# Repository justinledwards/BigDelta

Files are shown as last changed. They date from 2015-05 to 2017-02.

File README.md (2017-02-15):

# BigDelta

A very large Delta 3D printer with very high precision and reliability that makes beautiful and accurate prints.
Chat at irc://chat.freenode.net/bigdelta

BOM: https://goo.gl/YLESNC
Mostly EU sourced BOM: https://goo.gl/JueIIJ

The Pudding: https://goo.gl/photos/vQzHpMG1wdQYkDLd6  

**Tools required:**
M5 tap, some oil for tapping.  M5 and M3 allen wrenches.  Wire cutters / strippers. 

**Recent:**
Added versions for 2040 Verticals and 4040 verticals.  Horizontal extrusion should be at 2040 for either.

**Tips:**
Instead of buying 1500mm x 2 for the horizontal extrusions you can buy 500mm x 6 to save some cutting.

**Onshape (CAD Files):**
https://goo.gl/xjHlLQ
https://goo.gl/zTKVrY

**Idler-nut-mod Onshape**
https://goo.gl/oGXj6e

**Build Photos:**
https://goo.gl/NL6L4Y
https://goo.gl/photos/2pFiowiZTJBhTSM98

----------

|Frame and Fastners|Quantity|Price Each|Price|Link|Notes|
| --- | --- | --- | --- | --- | --- |
|Solid Wheel Kit|9|$4.85|$43.65|http://openbuildspartstore.com/solid-v-wheel-kit/||
|Wheel Bolts 30mm M5 (25 pack)|1|$4.35|$4.35|http://openbuildspartstore.com/low-profile-screws-m5/||
|6mm Alu Spacers|6|$0.20|$1.20|http://openbuildspartstore.com/aluminum-spacers/||
|Eccentric spacers full size 6mm|3|$2.00|$6.00|http://openbuildspartstore.com/eccentric-spacer/||
|80mm gantry plate|3|$12.00|$36.00|http://openbuildspartstore.com/v-slot-gantry-plates/||
|1500mm 2040 extrusion|5|$19.50|$97.50|http://openbuildspartstore.com/v-slot-linear-rail/|Can get black or silver in 2040, 4040 vertices are available as well as 2040\. You can use 4040 for more rigidity|
|Endstops|3|$4.50|$13.50|http://openbuildspartstore.com/micro-limit-switch-kit-with-mounting-plate/|reliable and highly repeatable|
|Long vertex bolts 40mm M5 (25 pack)|1|$4.90|$4.90|http://openbuildspartstore.com/low-profile-screws-m5/|Doesn't hurt to buy an extra pack|
|Short vertex bolts 10mm M5 (25 pack)|2|$3.15|$6.30|http://openbuildspartstore.com/low-profile-screws-m5/|Again doesn't hurt to buy extra|
|18" Glass Build Plate|1|$47.99|$47.99|http://amzn.to/1Q1Ltjk||
|5 pack of the best steppers|1|$49.99|$49.99|http://www.ebay.com/itm/5pcs-NEMA17-BIPOLAR-STEPPER-MOTOR-76-oz-in-for-3D-Printer-ship-from-chicago-/181582676246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|You'll only need 3, but might as well have extra, you'll find a use for them|
|GT2 belt by the meter|6|$1.80|$10.80|http://www.robotdigg.com/product/10/Open+Ended+6mm+Width+GT2+Belt||
|Idler Pulley|3|$1.80|$5.40|http://www.robotdigg.com/product/383/6mm+wide+belt+idler+pulley+wheel+5mm+bore||
|16 tooth GT2 gear|3|$1.80|$5.40|http://www.robotdigg.com/product/59/Rostock-16-Teeth-5mm-Bore-GT2-Pulley||
|Post assembly T-Nuts (100 pack)|1|$7.50|$7.50|http://www.robotdigg.com/product/237|Not necessary, but makes life a lot easier|
|Pre assembly T-nuts (100 pack)|1|$8.00|$8.00|http://www.robotdigg.com/product/317/Pre+Assembly+T+Nuts+for+2020+Aluminum+Extrusion||
|18" strong rod kit|1|$25.69|$25.69|http://www.tridprinting.com/Mechanical-Parts/#3D-Printer-Rod-Kit||

----------

|Hotend|Quantity|Price Each|Price|||
| --- | --- | --- | --- | --- | --- |
|Genuine J-Head Hotend MK8|1|$56.99|$56.99|https://www.hotends.com/index.php?route=product/product&product_id=88|Specify MK8 in the order comments for the latest model, one of those things you shouldn't go cheap on|
|25mm metal fan|1|$1.80|$1.80|http://www.robotdigg.com/product/318/2510+12V+0.1A+DC+Fan|More never hurts|
|5015 blower parts fan|1|$1.80|$1.80|http://www.robotdigg.com/product/320/5015+12VDC+0.23A+Blower+Fan|More never hurts|

----------

|Extruder|Quantity|Price Each|Price|||
| --- | --- | --- | --- | --- | --- |
|Nema 11 27:1 geared stepper|1|$31.76|$31.76|http://www.omc-stepperonline.com/gear-ratio-271-planetary-gearbox-dual-shaft-nema-11-stepper-11hs120674dpg27-p-133.html|Might want to order 2 since shipping costs a bit|
|Tatsu V2 6mm ID Drive gear|1|$25.00|$25.00|http://deezmaker.com/store/#!/Tatsu-v2-Drive-Gear-Hobbed-Filament-Drive-Gear/p/24043350|Price sounds ridiculous, but it's worth it when you see it and use it, same as above|
|Spearfishing latex tubing|1|$14.23|$14.23|http://amzn.to/1Q1Lwvg||
|PTFE Tubing 4mm OD|1|$8.33|$8.33|http://www.ebay.com/itm/2-meters-PTFE-Teflon-Tube-For-1-75mm-Filament-for-3D-Printer-RepRap-Rostock-/261689172537||

----------

|Make your choice|Quantity|Price Each|Price|||
| --- | --- | --- | --- | --- | --- |
|Smoothieboard|0|$134.97|$0.00|http://shop.uberclock.com/collections/smoothie/products/smoothieboard-4x|Made by the original developers, only 1/16th microstepping|
|Azteeg X5 Mini|0|$109.00|$0.00|http://www.panucatt.com/azteeg_X5_mini_reprap_3d_printer_controller_p/ax5mini.htm|Uses smoothieware, not made by the original developers, a little crowded, but 1/32 microstepping, no networking|

----------
|Others|Quantity|Price Each|Price|||
| --- | --- | --- | --- | --- | --- |
|Zip ties|0|$0.00|$0.00||amazon by the box|
|M3 socket cap screws|||$0.00||amazon by the box|
|M3 nuts and nyloc nuts|||$0.00||amazon by the box|
|Powersupply 12V|0|$0.00|$0.00|http://amzn.to/1LPI4wd|You can use an ATX PSU that you already have, or get a dedicated 12V 30A PSU|
|Good filament 1.75mm PLA 1KG rolls|0|$30.00|$0.00|http://atomicfilament.com/|Check on #reprap on freenode for discounts|
|Glue-All Interior|1|$6.71|$6.71|http://amzn.to/1LPHP46||
|Printed Parts|1|$0.00|||Nearest & Dearest|
|Wires|||||Need 4 wires for each stepper, 2 wires for each endstop, 2 thicker wires for hotend, 2 wires for fans|
|Electronics fan|||||Doesn't hurt to have a fan go over your control board|
|2 part epoxy|||||for building rods|
|**Total**|||**$520.79**|||

PTCs http://amzn.to/1LPHxub

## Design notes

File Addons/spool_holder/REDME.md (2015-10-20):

Required Stuff:

1x Threaded rod (5/16 or 8mm) -- length contingent on extrusion length
2x 608zz Bearings
2x M8 or 5/16 lock nuts
2x M8 or 5/16 nuts

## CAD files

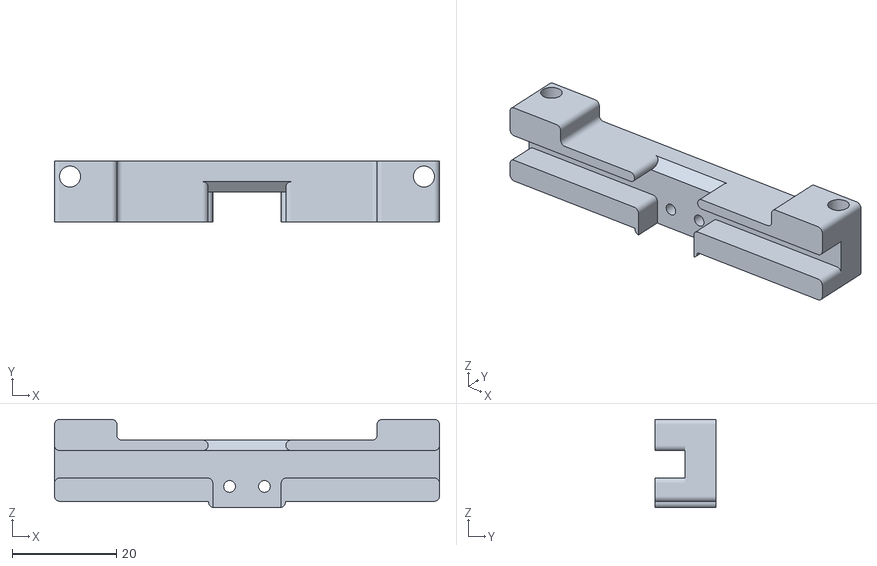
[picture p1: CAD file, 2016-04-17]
Addons/Magnetic_Probe.stl
74.0 x 11.8 x 17.0

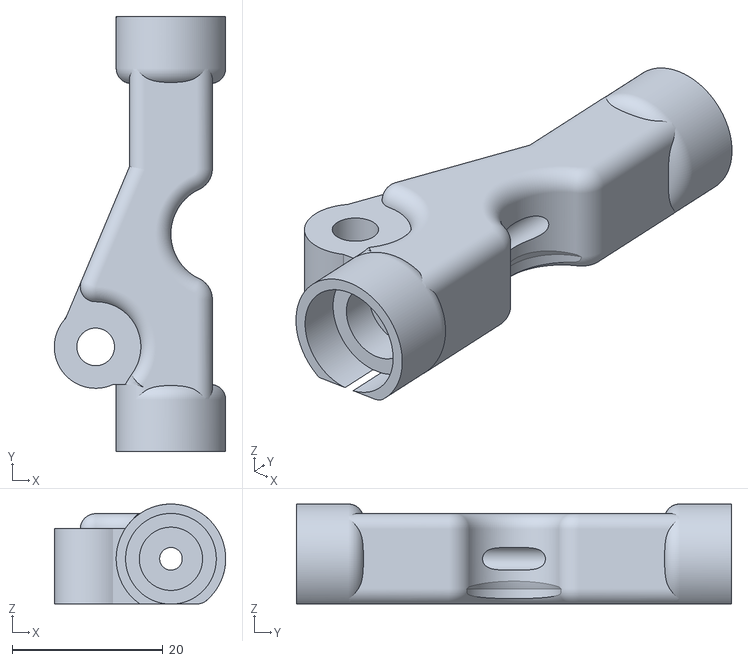
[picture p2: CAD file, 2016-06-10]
Addons/metal_tube_extruder/Rework Metal Tube Extruder - TubeHolder.stl
22.8 x 57.8 x 13.3

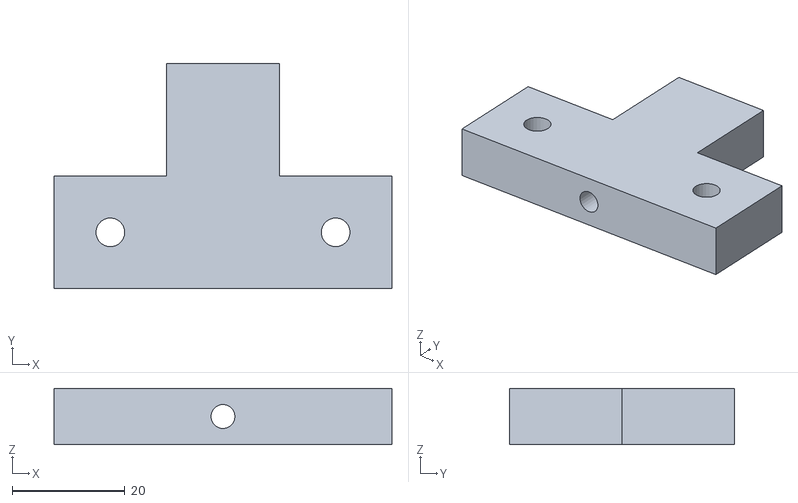
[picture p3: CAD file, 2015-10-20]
Addons/spool_holder/guide.stl
60.0 x 40.0 x 10.0

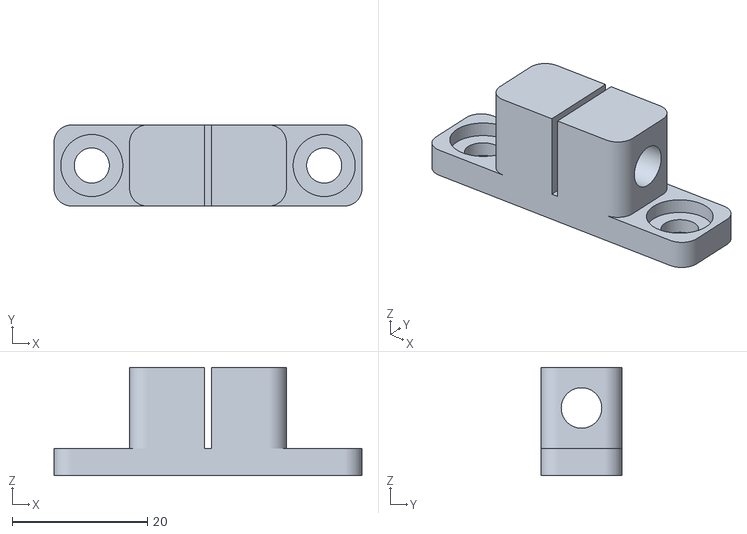
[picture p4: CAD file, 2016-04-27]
Misc-tools/Rod Jigs - Rod Cutter Jig.stl
45.6 x 12.0 x 16.0

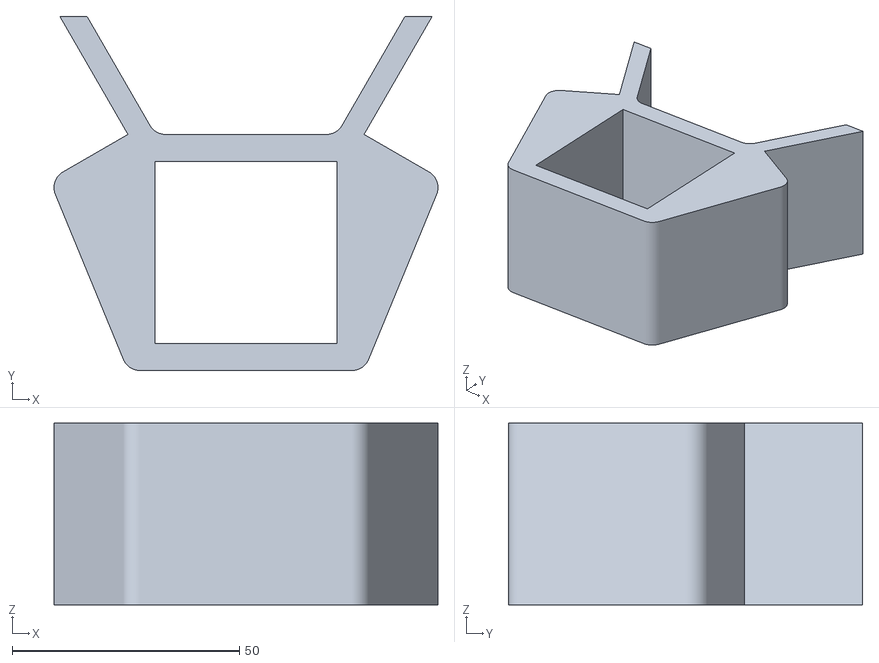
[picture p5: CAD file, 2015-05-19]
original_build/Vertex - Part 1.stl
84.6 x 78.0 x 40.0

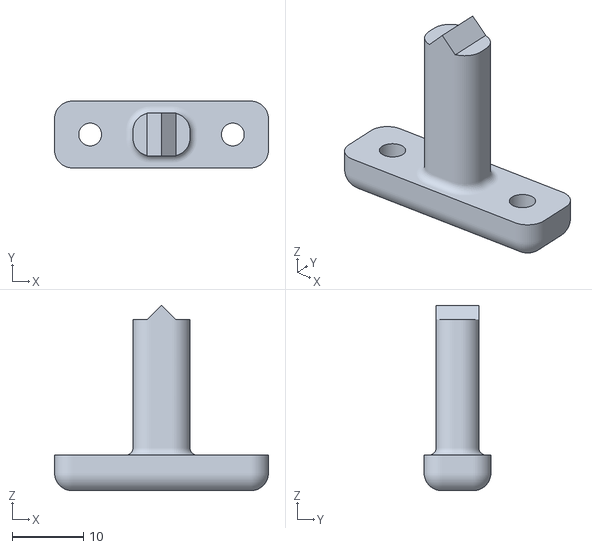
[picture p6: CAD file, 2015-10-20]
Sextruder-Idler.stl
30.0 x 9.38 x 26.0

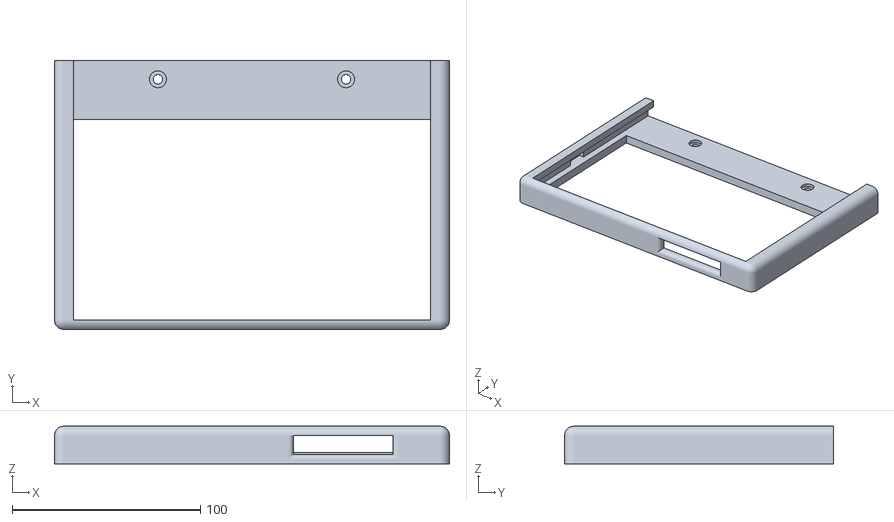
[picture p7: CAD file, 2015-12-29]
Addons/Nexus-7-Holder.stl
210.0 x 143.0 x 20.0

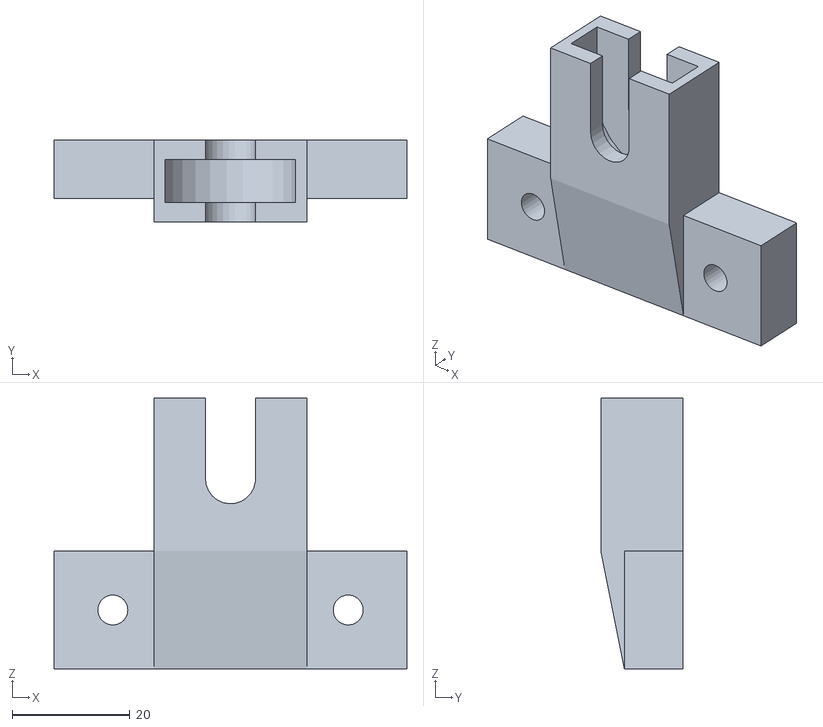
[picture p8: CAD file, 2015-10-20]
Addons/spool_holder/holder_for_extrusion.stl
60.0 x 14.0 x 46.0

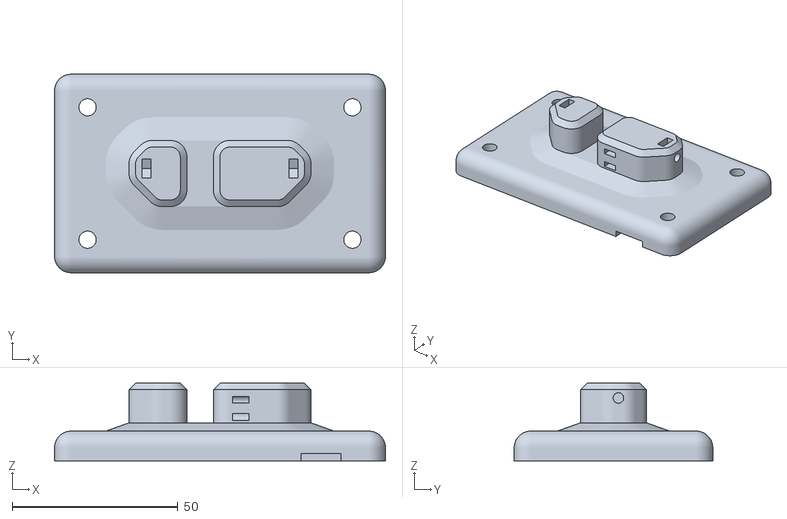
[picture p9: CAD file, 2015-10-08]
Carriage.stl
100.0 x 60.0 x 23.5

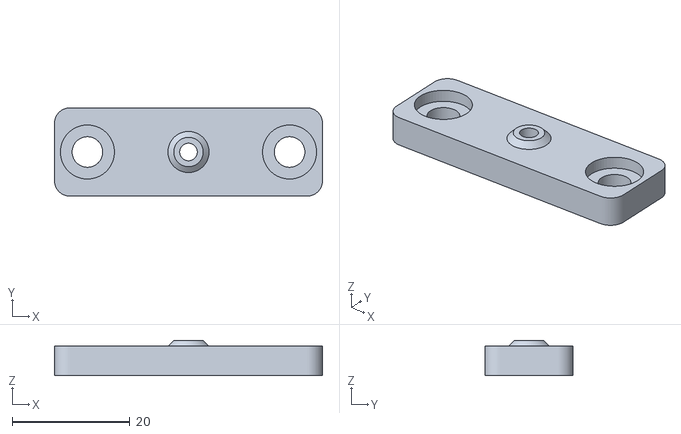
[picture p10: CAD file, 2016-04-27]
Misc-tools/Rod Jigs - Rod Glue Jig.stl
45.6 x 15.0 x 6.00

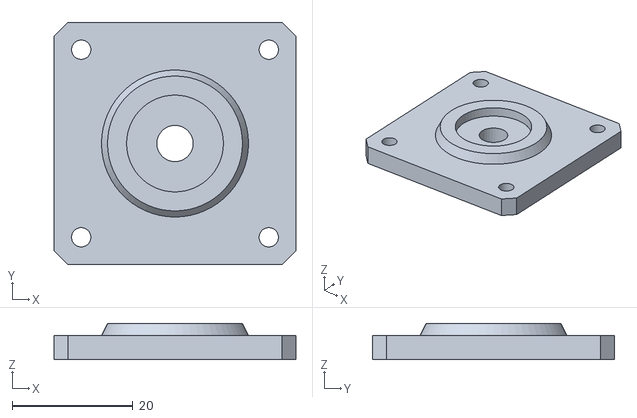
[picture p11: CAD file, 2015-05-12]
original_build/vertex_20x40_idler_cap.stl
40.0 x 40.0 x 6.00

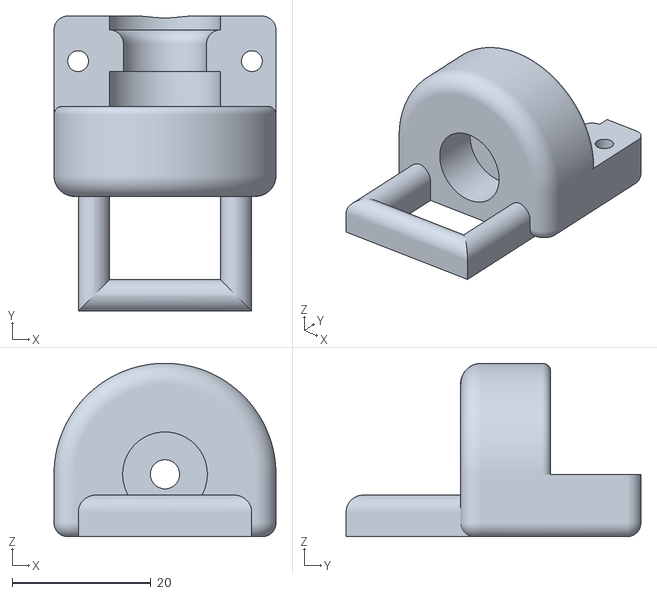
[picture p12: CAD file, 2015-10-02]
Addons/Effector-E3D-Volcano-Clamp.stl
32.0 x 42.5 x 25.0

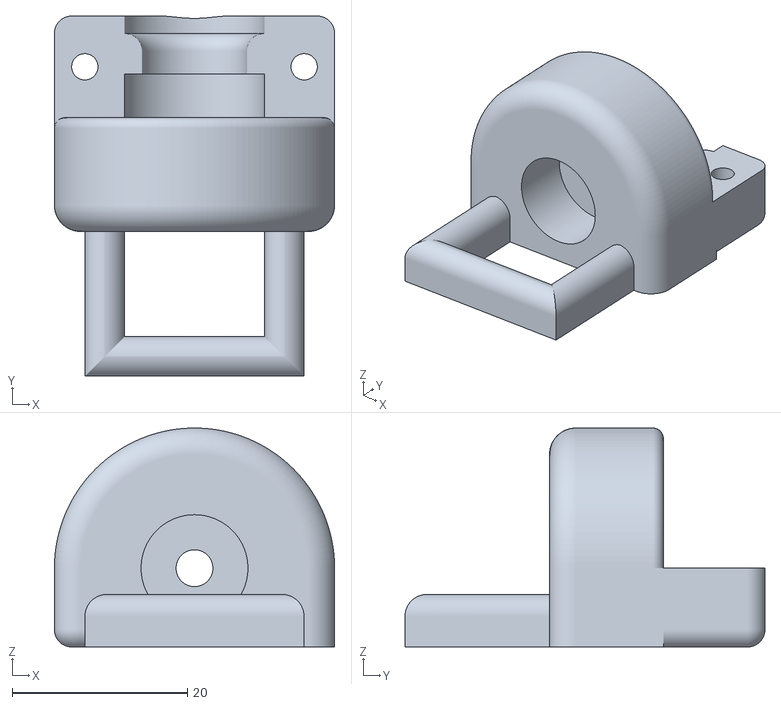
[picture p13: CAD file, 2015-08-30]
Effector-Hotend_Clamp.stl
32.0 x 41.1 x 25.0

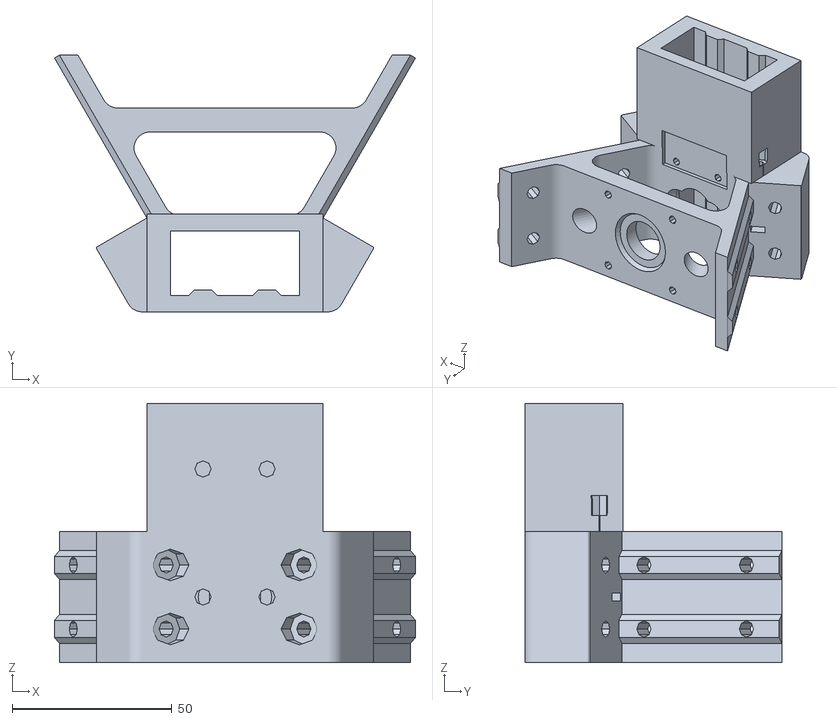
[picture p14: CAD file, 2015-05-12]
original_build/vertex_20x40-Beefy.stl
112.8 x 80.3 x 81.0

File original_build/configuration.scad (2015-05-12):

// Delta-Six 3D Printer 
// Created by Sage Merrill
// Released on Openbuilds.com
// Based on orginal design by Johann C. Rocholl (Kossel Printer)
// License = Attribution Share Alike - CC BY SA


include <metric_fastners.scad>;
use <nema17.scad>;
use <beam.scad>;
use <timing_belts.scad>;

$fn=20;

// Increase this if your slicer or printer makes the holes too small.
extra_radius = 0.10;
extra_boolean = 0.15;

// Delta Parameters
global_delta_arm_seperation = 55;
global_effector_bore_radius = 21;
global_mounting_hole_radius = 27;

// M5 Hardware
m5_bolt = m5_major_radius*2;
m5_bolt_boolean = m5_bolt+extra_radius;

// M3 Hardware
m3_bolt = m3_major_radius*2;
m3_bolt_boolean = m3_bolt+extra_radius;

// NEMA17 stepper motor
motor_length = 47.5;
motor_shaft_radius= 5.00/2;

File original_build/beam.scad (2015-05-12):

// Misumi Beam
module misumibeam(size1=15, size2=15, length=100, extra=0.1) {
   difference() {
      cube([size1+extra, size2+extra, length], center=true);
      for (a = [0:180:180]) rotate([0, 0, a]) {
         translate([size1/2, 0, 0]) {
          //  % cube([size1/2, 3, length+1], center=true);
			minkowski() {
               cube([size1/2-(extra+1), size1/6-extra, length+1], center=true);
               cylinder(r=0.5, h=1, center=true);
			} 
        }
      }
      for (a = [0:90:270]) rotate([0, 0, a]) {
         translate([size2/2, 0, 0]) {
          //  % cube([size1/2, 3, length+1], center=true);
			minkowski() {
               cube([size1/2-(extra+1), size1/6-extra, length+1], center=true);
               cylinder(r=0.5, h=1, center=true);
			} 
        }
      }
   }
}

# misumibeam(15, 15, 300);

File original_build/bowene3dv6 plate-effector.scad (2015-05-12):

fudge = 0.2;
plate_width = 58;
plate_depth = 28;
plate_height = 6;
top_diameter = 16;
grovemount_diameter = 12;
mount_hole_width = 54;
mount_hole_dia = 3;
translate([15,10,3])
rotate([90,180,0])

good_holder();


difference(){
//import("bowden_v1.4_E3D_V6.stl");
//mount_holes();

}

module cap_bolt_boolean(dia,len,fn=8)
{
	e=1.87*dia;
	h1=2*dia;
	cylinder(r=dia/2,h=len,$fn=fn);
	translate([0,0,-h1+0.05]) cylinder(r2=e/2+0.15,r1=e/2+0.3,h=h1,$fn=fn);
}

module main_plate()
{
  cube([plate_width-fudge,plate_depth-fudge,plate_height-fudge], center=true);
}

module mount_holes()
{
for (a = [0:30:360]) rotate([0, 0, a]) {
		translate([0, 27, 10]) rotate([0, 180, 0])
		 cap_bolt_boolean(3, 20);
	 }  


//translate([mount_hole_width/2,0,0])
//   cylinder(d=mount_hole_dia+fudge, h=plate_height+100, center=true);
//  translate([mount_hole_width/-2,0,0])
//   cylinder(d=mount_hole_dia+fudge, h=plate_height+100, center=true);
}
module grove_mount()
{
cylinder(d=grovemount_diameter+fudge, h=plate_height+1, center=true);
translate([0,plate_depth/2-grovemount_diameter/2,0])
cube([grovemount_diameter+fudge,plate_depth/2+1,plate_height+1], center=true);

}


module good_holder()
{
difference(){
union(){
translate([0,0,(plate_height/2)-(fudge/2)+3.5])
cylinder(d=top_diameter+3,h=7, center=true);
translate([0,0,11.2])
cube([plate_width-fudge,plate_depth-fudge,3], center=true);
}
mount_holes();

translate([0,0,4.4])
cylinder(d=top_diameter,h=3, center=true);
translate([0,0,(plate_height/2)-(fudge/2)+2])
cylinder(d=10,h=50, center=true);

}
}






*difference(){
main_plate();
mount_holes();
grove_mount();
};

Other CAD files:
Addons/endstop-holder.stl
Addons/spool_holder/locking_cone.stl
original_build/carriage_20x40-testing.stl
Addons/bed_holder.stl
original_build/brace.scad
Addons/spool_holder/holder_for_tap_holes.stl
Addons/spool_holder/locking_screw.stl
original_build/brace.stl
original_build/carriage_20x40-testing.scad
original_build/carriage_20x40.scad
original_build/carriage_20x40.stl
original_build/carriage_20x40_backplate.stl
original_build/carriage_20x40_template.stl
original_build/effector.scad
original_build/effector.stl
original_build/effector_light_ring.stl
original_build/light_ring_mount.scad
original_build/metric_fastners.scad
original_build/nema17.scad
original_build/plastic_t_nut.scad
original_build/test-plate.scad
original_build/timing_belts.scad
original_build/vertex_20x40.scad
original_build/vertex_20x40.stl
original_build/vertex_20x40_idler_cap.scad

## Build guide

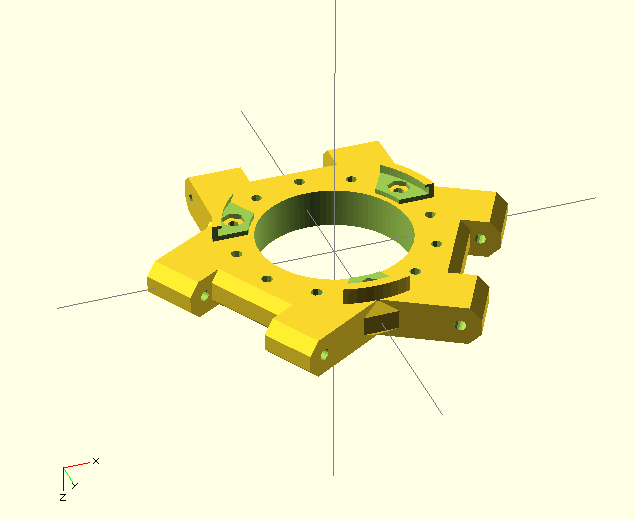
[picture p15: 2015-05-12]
original_build/effector.png

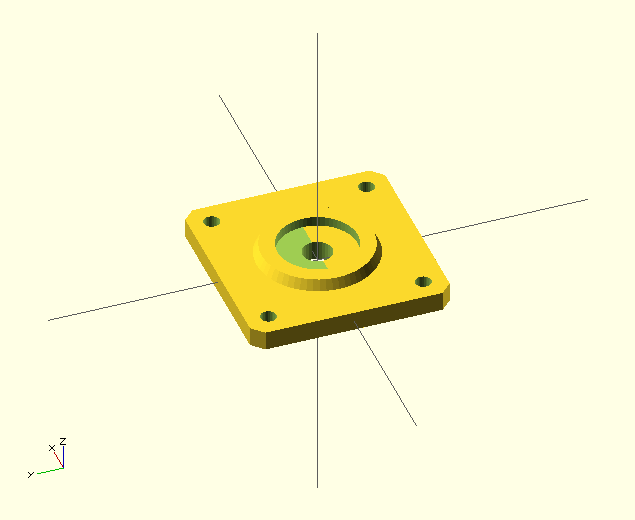
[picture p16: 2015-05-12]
original_build/vertex_20x40_idler_cap.png

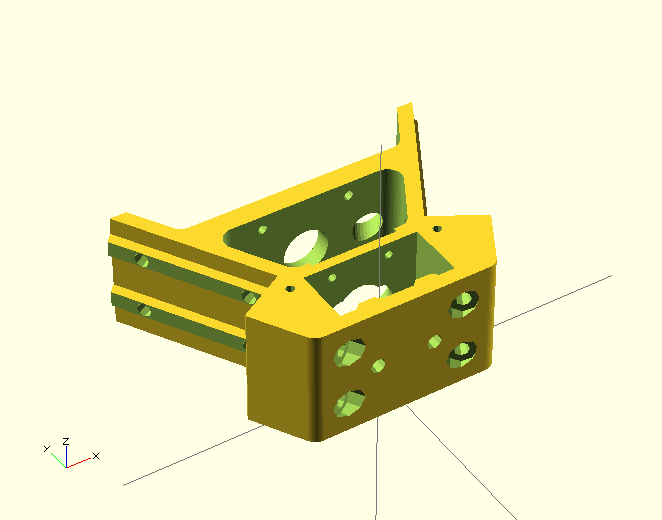
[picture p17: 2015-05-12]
original_build/vertex_20x40.png

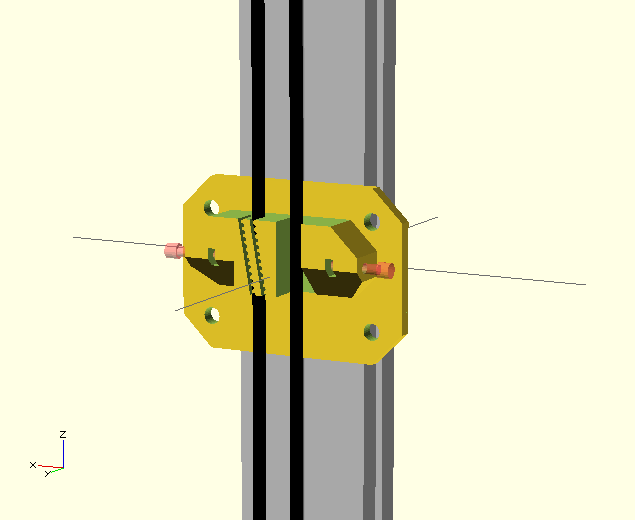
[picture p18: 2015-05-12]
original_build/carriage_20x40.png

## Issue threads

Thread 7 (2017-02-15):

Clearance for counterbored side end bolts

thehans, 2017-02-15:
I'm having difficulty getting the bolt heads to fit in the counterbored holes of the vertex piece.  It seems that there is no clearance designed into the part.  I've have to drill all my vertex parts out for the bolts to fit.

It looks like the holes in the part design are 9mm ID.  I printed parts at 0.25mm layer height, and the first bridged layer of the holes can sometimes sag a bit, which makes the hole effectively even smaller.

I have some of the ultra low profile openbuilds M5 bolts and they have 9.25mm diameter head.  I also have some M5 socket button head cap screw from McMaster and they are 9.5mm diameter.  I also checked a hex head cap screw which was 9mm at its widest.

Can the parts be changed so that the widest bolt head (9.5mm) will fit, and plus a few tenths of a mm for added clearance.  I think 10mm would be a nice round number.

justinledwards, 2017-02-15:
@thehans

I haven't talked to others yet, but it wouldn't be too difficult to turn those things into parameters.  Until something like that is done, I wanted to show where the sketch dimensions are at so you can modify them.

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

As these were designed early on in onshape, not all features were available yet and it could be cleaned up quite a bit.

justinledwards, 2017-02-15:
I added a variable that you can adjust.

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

Closed 2017-02-15.

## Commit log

2015-05-12 pushing out old files
    [beam.scad, bowene3dv6 plate-effector.scad, brace.scad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]
2015-05-19 4040 vertex
    [Vertex - Part 1.stl]
2015-08-30 origina_build folder created
    [Vertex - Part 1.stl, beam.scad, bowene3dv6 plate-effector.scad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]
2015-08-30 Adding 4040 Files
    [Vertex - Part 1.stl, beam.scad, bowene3dv6 plate-effector.scad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]
2015-08-30 Added Carriage
    [Carriage.stl]
2015-08-30 Effector added
    [Effector-Hotend_Clamp.stl]
2015-08-30 Added Sextruder
    [Sextruder-Idler.stl]
2015-09-14 2040 Idler Added
2015-09-15 Add bed holder...
    [bed_holder.stl]
2015-09-16 Implemented carriage design with horizontal slot for ziptie to attach directly
    [Carriage.stl]
2015-09-16 Beefed up belt gripper pillar and zip tie gripper pillar to 3.25x5mm
    [Carriage.stl]
2015-09-16 Add optional endstop holder to avoid buying endstop kit from openbuilds
    [endstop-holder.stl]
2015-10-02 clamp for volcano
    [Effector-E3D-Volcano-Clamp.stl]
2015-10-08 Carriage netfabbed
    [Carriage.stl]
2015-10-20 Spool holder added
    [holder_for_extrusion.stl, holder_for_tap_holes.stl, locking_cone.stl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]
2015-10-20 updated sextruder idler
    [Sextruder-Idler.stl]
2015-10-20 added fila guide
    [guide.stl]
2015-12-29 Added Nexus 7 (2013) holder
    [Nexus-7-Holder.stl]
2016-01-15 Updated effector duct
2016-01-21 Added Chopped Slot STLs
2016-02-03 Added support for a lock nut for the idler bolt
2016-04-08 Rotated nut hole to improve overhang
2016-04-16 Added mostly EU BOM
2016-04-17 Magnetic Probe https://goo.gl/4hAJNY
    [Magnetic_Probe.stl]
2016-04-25 Added some tools for building the printer
    [Rod Jigs - Rod Cutter Jig.stl, Rod Jigs - Rod Glue Jig.stl]
2016-06-10 metal tub etruder from https://cad.onshape.com/documents/a3cb8db7b43254e191f1baf0/w/6af71ddfbe1a12a952c95254/e/e7b23ea0ffae0b05dfb65ede
    [Rework Metal Tube Extruder - TubeHolder.stl]
